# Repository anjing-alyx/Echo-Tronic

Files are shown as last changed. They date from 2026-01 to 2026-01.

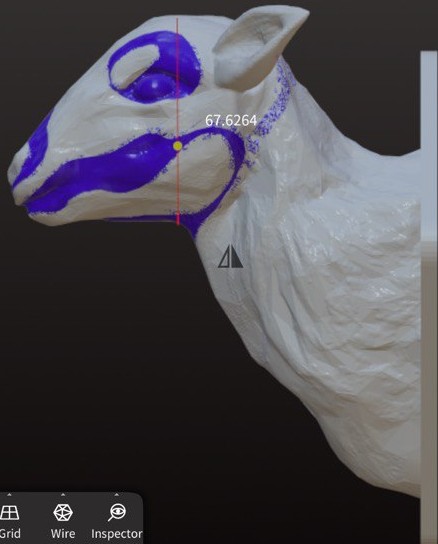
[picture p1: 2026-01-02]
Concept Art/NomadSculpt.jpg

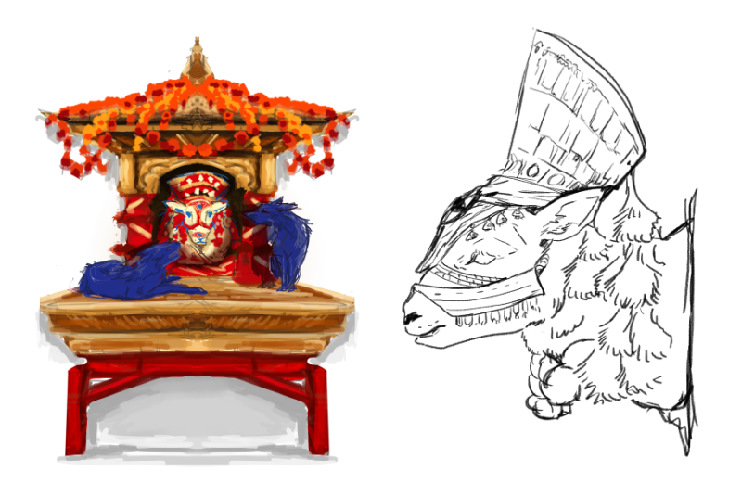
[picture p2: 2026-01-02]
Concept Art/Lamb_worship_conceptart.png

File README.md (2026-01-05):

README [WIP]
Translating human facial motion into physical animatronic movement in real time using Mediapipe API, Arduino and PCA9865. 

1. [What is Echo-Tronic](#What-is-Echo-Tronic)

2. [How does it work](#How-does-it-work)
<br/> 2.1 [Hardware](##Hardware)
<br/> &nbsp; 2.1.1 [Echo-Tronic (a.k.a AnimaBarong) Design](##Echo-Tronic-(a.k.a-AnimaBarong)-Design)
<br/> &nbsp; 2.1.2 [Arduino and PCA9685](###Arduino-and-PCA9685)
<br/> 2.2 [Software](##Software)
<br/> &nbsp; 2.2.1 [Servo Angle Calculation](###Servo-Angle-Calculation)
<br/> &nbsp; 2.2.2 [MediaPipe Facial Tracking](###MediaPipe-Facial-Tracking)
<br/> &nbsp; 2.2.3 [Arduino Serial Communication](###Arduino-Serial-Communication)

3. [What is included](#What-is-included)

4. [Final Notes:](#Final-Notes)

# What is Echo-Tronic:
Echo-Tronic (a.k.a AnimaBarong) is a personal project intending to simplify animatronic facial control from 2-4 operators controlling various facial features to one animatronic rig "echoing" an actor's performance using facial tracking. In a standard rig for facial animatronics there may be 6-20+ servos depending on complexity of expression. As humans only have two hands and 10 fingers, to control 20+ servos simultaneously using RC controllers is a bit tricky- hence the 2-6+ puppeteers manning an animatronic. 

The goal of this project is to reduce manpower required to operate animatronics, allow for more organic acting/performance, and moving the servos in real-time. This, of course, also has use in the field of social robotics and human-robot interaction- however, theme park animatronics for the use case is much more fun. 

# How does it work:
## Hardware
### Echo-Tronic (a.k.a AnimaBarong) Design
The design for the animatronic initially came from a character of mine based on the [Balinese Barong](https://en.wikipedia.org/wiki/Barong_(mythology)) hence the "a.k.a", it has since changed to a sheep head which was inspired by Weta's work on the [Black Sheep Movie](https://www.wetaworkshop.com/projects/black-sheep) and the internal mechanisms based on Gustav Hoegan's work on a [Bison head in a super glue advert](https://www.biomimicstudio.org/showreel). 

All the internal structures were modelled and assembled on SolidWorks as well as 3D printed using a Bambu X1C and PLA Filament. Non-printed parts include:
1. MG90S servos (x11)
2. Various M2.5-M3 Screws
3. Paperclips and wires
4. Electronics

The internal structure was based of a lamb head I sculpted on NomadSculpt for the next step which is a test-skin. But this is an engineering documentation not model-making documentation- so I will leave the foam skin for later. The design goal was to create a modular structure that was easy to assemble and reassemble for repairs while being easy to fabricate both on the 3D printer and machine (although that part remains to be optimized). 

### Arduino and PCA9685
I use Arduino as my testbed and PCA to control my 11 servos. They are great tools for testing- plus the only things available at home.

## Software
### Servo Angle Calculation
Initially this was done via inverse kinematics however the way euclidean distance was calculated provided inaccurate results- hence why a ratio based method was used with some hard-coded distances set in the code to calculate the servo angles. The simple calculation basically allowed for easier tuning (provided you know how to code) and less computation. I also rounded each of the angles calculated to integers that were either multiples of 2 and 5 to reduce the sensitivity of the servos when moving. 

In the future, potentially for more advanced social robots with feedback loops and the need for reliable/adaptive movement- inverse kinematics with servo feedback will be used. 

### MediaPipe Facial Tracking
[MediaPipe Face Landmark Recognition](https://ai.google.dev/edge/mediapipe/solutions/vision/face_landmarker) is the machine learning portion that detects the face and provides the coordinates for facial tracking. The distance between points such as the most top and most bottom part of the eye, is now used to calculate approximately how much the servo moves. 

<p align="center">MP Face Mesh with indices</p>
<p align="center">Fig. 1 MediaPipe Face Mesh with Indices Reference </p>

### Arduino Serial Communication
For now, the head still had an umbilical cord to the computer for control however since what Python sends via serial connection is a 22 bit string of servo angles, the order of which is associated to the servos pin-outs on the PCA9685. This packet of information can theoretically be wirelessly transmitted via RC which is the future plan of the work. 

# What is included
In this repository what is included is the most up to date working code and the .stl files for the animatronic hardware. No Solidworks Files will be shared.

# Final Note
Have fun looking around, this is ultimately a passion project in the somewhat declining trade of animatronics and sfx in movies. If you do use this as inspiration or the code for whatever reason, please credit and let me know because I'd love to see where it ends up. There are still a lot of bugs I am fixing as an amateur coder; sorry in advance- I'll fix them soon or whenever I get the time to!

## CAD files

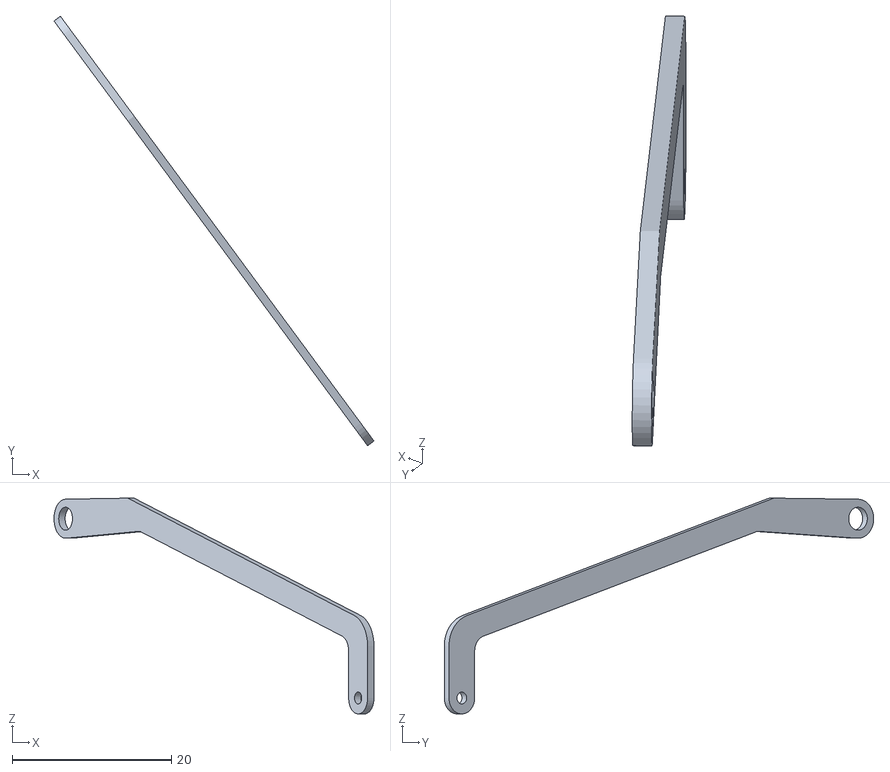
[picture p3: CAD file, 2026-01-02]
Hardware Files/Eye Assembly/EYE_LINKAGE_L.STL
40.1 x 53.9 x 27.1

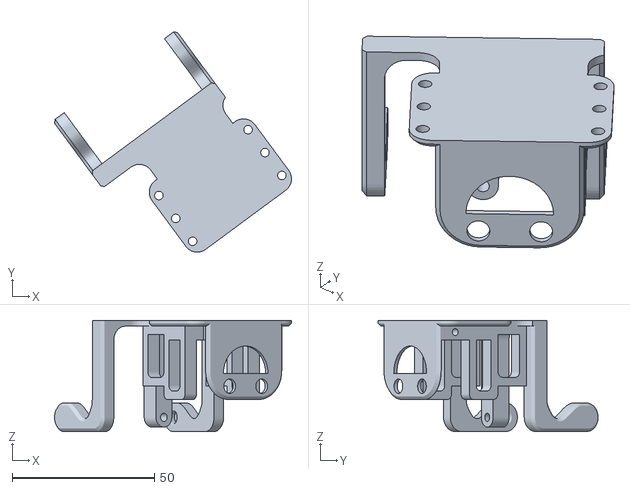
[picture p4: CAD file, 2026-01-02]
Hardware Files/Eye Assembly/Mirror/M_EYE_SERVOHOLDER.STL
83.4 x 77.5 x 39.0

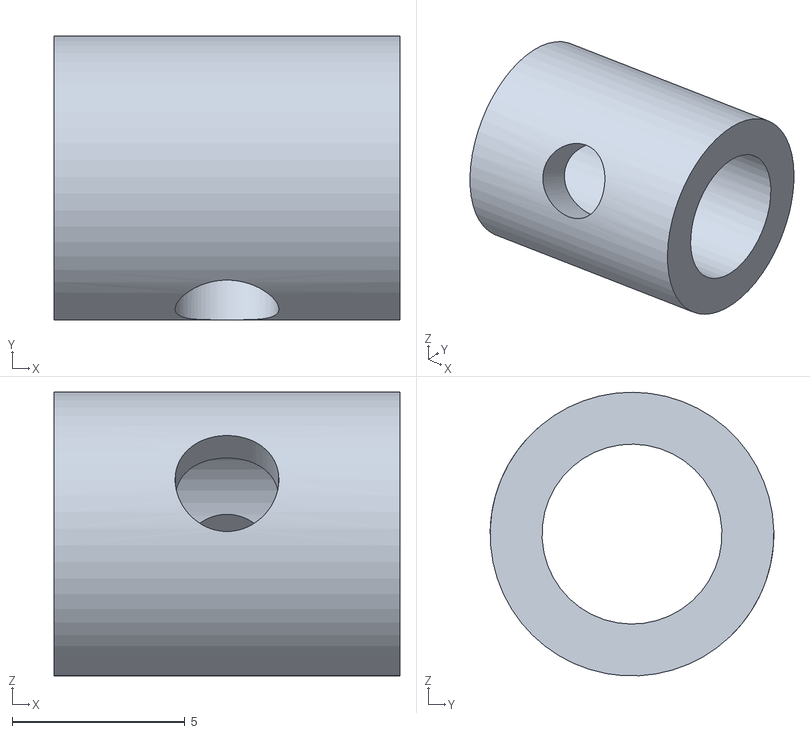
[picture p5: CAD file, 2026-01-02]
Hardware Files/LOWER JAW ROD SPACER.STL
10.0 x 8.20 x 8.19

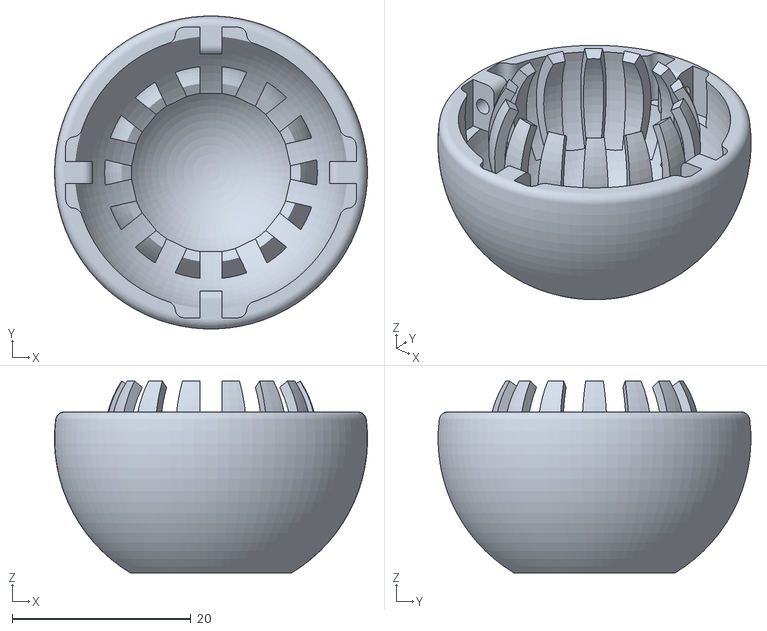
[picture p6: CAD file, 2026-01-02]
Hardware Files/Eye Assembly/EYE_EYEBALL.STL
35.0 x 35.0 x 21.4

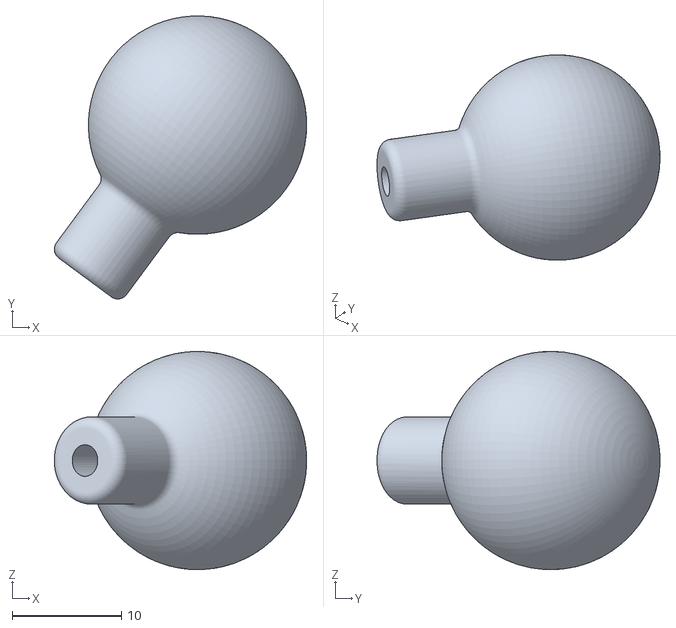
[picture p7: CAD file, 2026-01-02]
Hardware Files/Eye Assembly/Mirror/M_EYE_BALLJOINT.STL
23.1 x 25.9 x 20.0

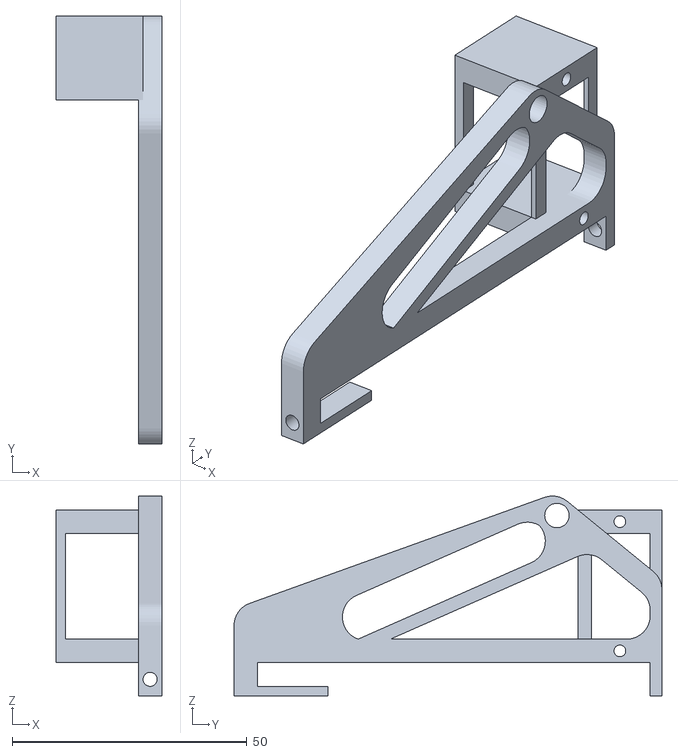
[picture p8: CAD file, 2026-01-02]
Hardware Files/M_LOWERJAW_SERVOHOLDER.STL
22.5 x 91.1 x 42.6

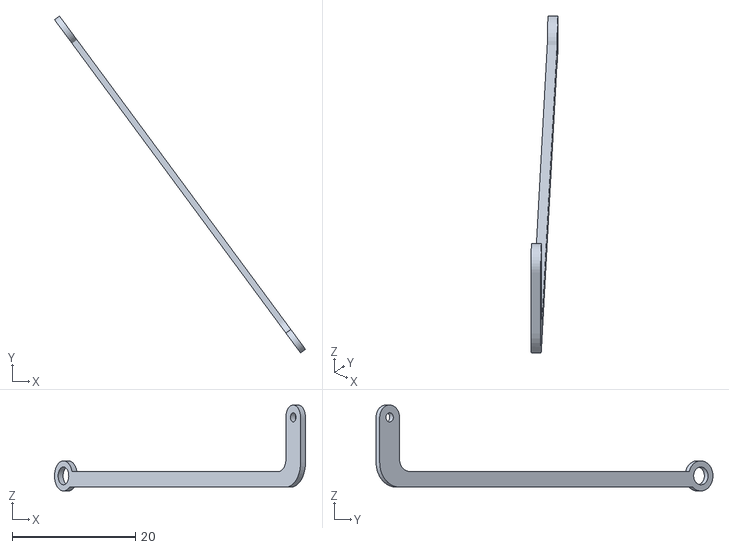
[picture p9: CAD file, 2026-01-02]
Hardware Files/Eye Assembly/EYE_LINKAGE_U.STL
40.7 x 54.6 x 13.9

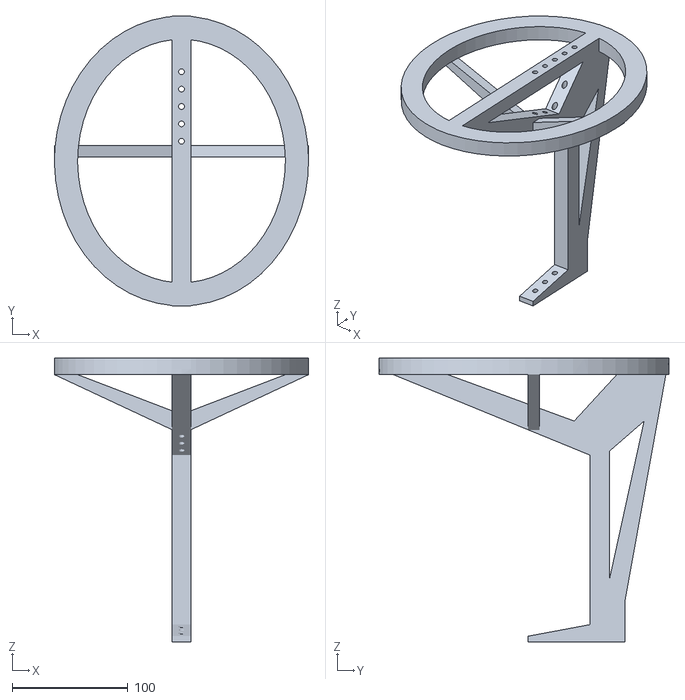
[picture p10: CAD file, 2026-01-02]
Hardware Files/TEMP_HEADSTAND.STL
219.2 x 250.0 x 245.0

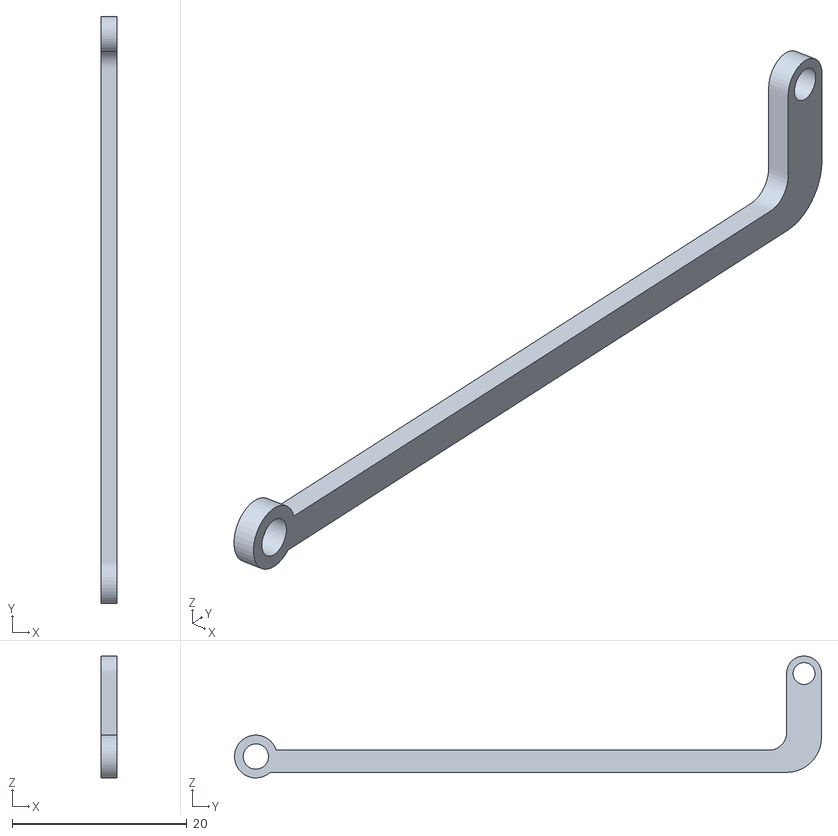
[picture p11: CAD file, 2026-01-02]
Hardware Files/Eye Assembly/EYE_EYELID_UPPER.STL
1.80 x 67.2 x 13.9

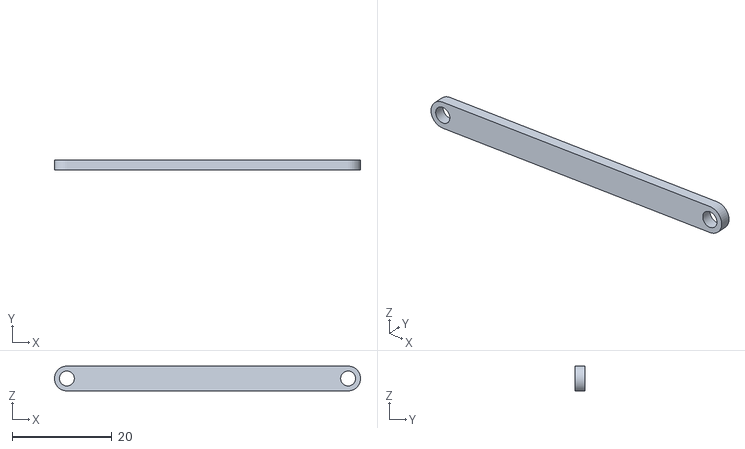
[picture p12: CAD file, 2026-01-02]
Hardware Files/NOSE_L3.STL
61.5 x 2.00 x 5.00

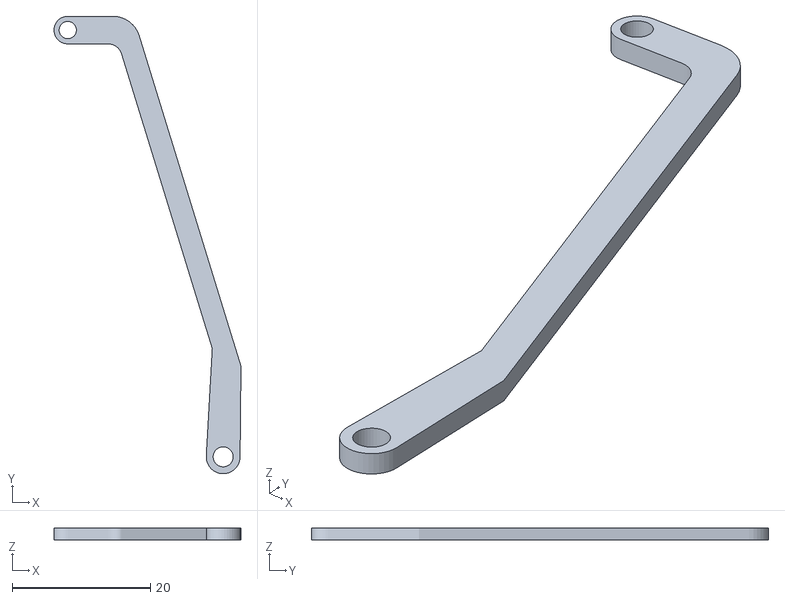
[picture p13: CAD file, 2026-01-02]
Hardware Files/Eye Assembly/EYE_EYELID_LOWER.STL
27.1 x 66.2 x 1.80

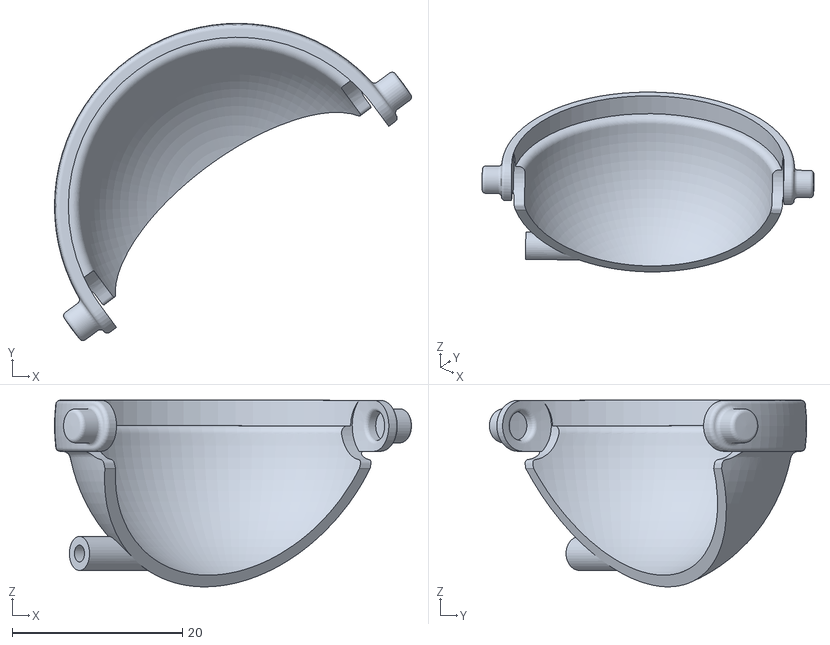
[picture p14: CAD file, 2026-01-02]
Hardware Files/Eye Assembly/Mirror/M_EYELID_UPPER.STL
41.9 x 37.3 x 21.9

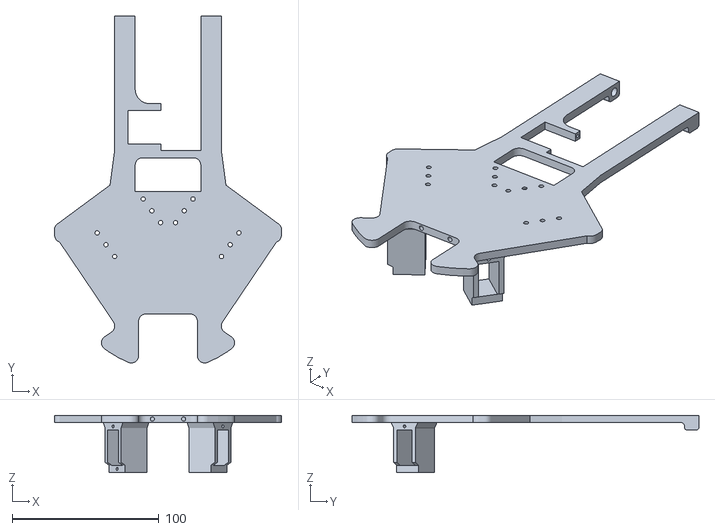
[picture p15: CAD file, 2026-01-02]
Hardware Files/HEAD_BASE.STL
154.9 x 236.4 x 39.0

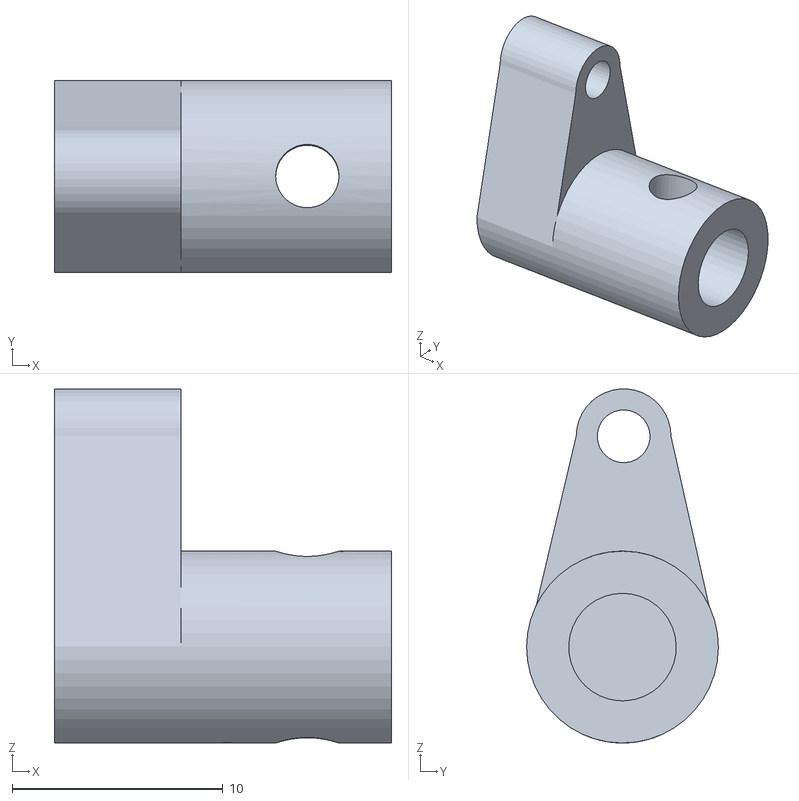
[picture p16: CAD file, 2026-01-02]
Hardware Files/LOWERJAW ROD HUB.STL
16.0 x 9.10 x 16.8

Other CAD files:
Hardware Files/EYEBROW_LINKAGE.STL
Hardware Files/Eye Assembly/EYE_SERVOHOLDER.STL
Hardware Files/Eye Assembly/Mirror/M_EYELID_LOWER.STL
Hardware Files/HEAD_MOUNT.STL
Hardware Files/LOWER JAW.STL
Hardware Files/LOWERJAW-SERVO LINKAGE.STL
Hardware Files/LOWERJAW_SERVOHOLDER.STL
Hardware Files/NECK.STL
Hardware Files/NOSE.STL
Hardware Files/NOSE_L2.STL

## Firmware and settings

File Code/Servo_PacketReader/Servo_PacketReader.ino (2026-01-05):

#include <Wire.h>
#include <Adafruit_PWMServoDriver.h>

Adafruit_PWMServoDriver pwm = Adafruit_PWMServoDriver(0x40);

#define SERVOMIN 125 // Minimum pulse length (0 degrees)
#define SERVOMAX 625  // Maximum pulse length (180 degrees)
#define N_SERVOS 11   // Total servos

void setup() {
  Serial.begin(115200);
  pwm.begin();
  pwm.setPWMFreq(50); // Servos ~50 Hz

  // Initialize all servos to neutral 90°
  for(int i=0; i<N_SERVOS; i++){
    pwm.setPWM(i, 0, angleToPulse(90));
  }
}

// Convert angle (0-180) to PWM pulse
int angleToPulse(int angle) {
  angle = constrain(angle, 0, 180);
  return map(angle, 0, 180, SERVOMIN, SERVOMAX);
}

void loop() {
  if(Serial.available()){
    static String buffer = "";
    char c = Serial.read();

    if(c == '<'){
      buffer = ""; // start marker
    } 
    else if(c == '>'){
      // end marker -> parse packet
      int count = 0;
      char *token = strtok((char*)buffer.c_str(), ",");
      while(token != NULL && count < N_SERVOS){
        int angle = atoi(token);
        pwm.setPWM(count, 0, angleToPulse(angle));
        token = strtok(NULL, ",");
        count++;
      }
    } 
    else {
      buffer += c;
    }
  }
}

/* Servo Mapping (Python packet indices):
   S0: ReyeX       -> Channel 0
   S1: LeyeX       -> Channel 1
   S2: ReyeY       -> Channel 2
   S3: LeyeY       -> Channel 3
   S4: Rblink      -> Channel 4
   S5: Lblink      -> Channel 5
   S6: Rebrow      -> Channel 6
   S7: Lebrow      -> Channel 7
   S8: Right Mouth -> Channel 8
   S9: Left Mouth  -> Channel 9
   S10: Nose       -> Channel 10
*/

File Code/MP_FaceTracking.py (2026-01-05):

# -*- coding: utf-8 -*-
"""
Created on Fri Dec 19 16:03:16 2025

@author: Adel Lee (SYK)
"""
import math
import serial
import time
import mediapipe as mp
import cv2
import tkinter as tk
from threading import Thread
import numpy as np

# ---------------------------
# Servo setup (angle and variable definition)
# ---------------------------
### Author's Note: Servo start angle/min angle is always in closed position. Left Servos are always mirrored ###

rx_min, rx_max = 72, 108 ## Right Eye X-Direction - Servo 0 (-)R, (+)L
lx_min, lx_max = 72, 108 ## Left Eye X-Direction - Servo 1 (-R), (+)L

ry_min, ry_max = 76.5, 103.5 ## Right Eye Y-Direction - Servo 2 (-)D, (+)U
ly_min, ly_max = 76.5, 103.5 ## Left Eye Y-Direction - Servo 3 (-)U, (+)D

rb_min, rb_max = 20, 90 ## Right Eye Blink - Servo 4 (-)U
lb_min, lb_max = 90, 140 ## Left Eye Blink - Servo 5 (+)U

reb_min, reb_max = 75, 105 ## Right Eyebrow - Servo 6 (-)D, (+)U  - Index 295 track relative to midpoint of eye_width
leb_min, leb_max = 75, 105 ## Left Eyebrow - Servo 7 - (-)U, (+)D - Index 55

m1_min, m1_max = 90, 180 ## Right Mouth Servo - Servo 8 (-)U, (+)D
m2_min, m2_max = 0, 90 ## Left Mouth Servo - Servo 9 (-)D, (+)US

nose_min, nose_max = 81,120 ## Nose Servo - Servo 10 (-)U, (+)D

## Define Horizontal Eye Distance as a scale bar for mm conversion ##
horizontal_eye = 32

SENSITIVITY = 6             # Max deviation from center, Adjust this setting to increase range of angle
SMOOTH_ALPHA = 0.9           # smoothing factor, Adjust this setting if smoothing is less or more needed 

# Calibration storage
calib = {"x_min": None, "x_max": None, "y_min": None, "y_max": None}

# Mediapipe
mp_face_mesh = mp.solutions.face_mesh

selected_indices = [386, 374, 145, 159, 13, 14, 393, 269,
                    33, 133, 362, 263, 468, 473, 282, 442,222,52]

# ---------------------------
# Serial setup (safe) 
# ---------------------------
SERIAL_PORT = 'COM5'   # change this as needed
BAUD = 115200

arduino = None
try:
    arduino = serial.Serial(SERIAL_PORT, BAUD, timeout=0.1)
    time.sleep(2)  # wait for Arduino reset
except Exception as e:
    print(f"Warning: couldn't open serial port {SERIAL_PORT}: {e}")
    arduino = None

def pack_send(packet):
    """Send packet to Arduino with start/end markers and integer angles.
       Packet is list/tuple of numeric values.
    """
    if arduino is None:
        # For debugging without Arduino connected
        print("Would send:", packet)
        return
    # Ensure integers and clamp 0-180 (typical servo range)
    ints = [max(0, min(180, int(round(x)))) for x in packet]
    msg = "<" + ",".join(map(str, ints)) + ">"
    try:
        arduino.write(msg.encode())
    except Exception as e:
        print("Serial write error:", e)
        
# ---------------------------
# Utility Functions
# ---------------------------
# Source - https://stackoverflow.com/a
# Posted by Alok Singhal, modified by community. See post 'Timeline' for change history
# Retrieved 2025-12-29, License - CC BY-SA 4.0, for "def myround" only

def myround(x, base=2):
    return base * round(x/base)

def eu_dist(p1, p2):
    x1, y1 = p1
    x2, y2 = p2
    return math.sqrt((x2 - x1)**2 + (y2 - y1)**2)


eye_max = {"L": 0.0, "R": 0.0}  # store per eye

def theta14(p1,p2,sf):
    mm_convert=sf*eu_dist(p1,p2)
    eye_ratio = (mm_convert/(0.6*horizontal_eye))*90
    print(eye_ratio)
    if eye_ratio < 30:
        return 90
    elif eye_ratio >= 100:
        return 170
    else:
        return myround(eye_ratio)+90

def scale_factor (coords):
    lcorner, rcorner = coords[33], coords[133]
    eye_width = rcorner[0] - lcorner[0]
    return horizontal_eye/eye_width

##Top lip as anchor/ground for eu-dist calculation.
def mouth(m1, m2, sf):
    mdist = eu_dist(m1, m2)
    mdist_mm = mdist*sf
    mangle = math.degrees(math.asin(mdist_mm/140))*3 ## 140mm is the Length of Current Mouth
    m1angle = m1_min + mangle # Right mouth angle      
    return myround(m1angle)

def eyebrow(brow, eye, sf, mi, ma):
    edist = eu_dist(eye,brow)
    eangle = (myround(edist*sf,base = 5)/(1.2*horizontal_eye))*abs(ma-mi)+mi-16
    if eangle < 90 and eangle > 85:
        return 90
    if eangle > 90:
        return ma
    else:
        return myround(eangle, base =5)
    
def nose(l1, l2, sf):
    ldist = eu_dist(l1, l2)
    ldist_mm = ldist*sf 
    return myround(math.degrees(math.asin(ldist_mm/65))*3 + nose_min) ## 65mm is length of nose pivot to servo (Length of nose linkage)


# ---------------------------
# Landmark Extraction
# ---------------------------

def get_landmarks(frame, face_mesh):
    h, w, _ = frame.shape
    rgb = cv2.cvtColor(frame, cv2.COLOR_BGR2RGB)
    results = face_mesh.process(rgb)
    coords = {}
    if results.multi_face_landmarks:
        for face_landmarks in results.multi_face_landmarks:
            for idx in selected_indices:
                lm = face_landmarks.landmark[idx]
                coords[idx] = (int(lm.x*w), int(lm.y*h))
    return coords

# ---------------------------
# Continuous Calibration
# ---------------------------

def update_calibration(iris_ratio):
    # iris_ratio = (x_ratio, y_ratio)
    x, y = iris_ratio
    if calib["x_min"] is None or x < calib["x_min"]: calib["x_min"] = x
    if calib["x_max"] is None or x > calib["x_max"]: calib["x_max"] = x
    if calib["y_min"] is None or y < calib["y_min"]: calib["y_min"] = y
    if calib["y_max"] is None or y > calib["y_max"]: calib["y_max"] = y

# ---------------------------
# Eye Tracking
# ---------------------------

def process_eye_tracking(coords, prev_angles, eye="left"):
    if eye == "left":
        lcorner, rcorner = coords[33], coords[133]
        iris = coords[468]
    elif eye == "right":
        lcorner, rcorner = coords[362], coords[263]
        iris = coords[473]

    # Avoid division by zero
    eye_width = rcorner[0] - lcorner[0]
    eye_height = rcorner[1] - lcorner[1]
    if eye_width == 0: eye_width = 1
    if eye_height == 0: eye_height = 1

    iris_x_ratio = (iris[0] - lcorner[0]) / eye_width
    iris_y_ratio = (iris[1] - lcorner[1]) / eye_height

    # Update calibration
    update_calibration((iris_x_ratio, iris_y_ratio))

    # Map to servo angles
    if None not in calib.values():
        norm_x = np.interp(iris_x_ratio, [calib["x_min"], calib["x_max"]],
                           [90-SENSITIVITY, 90+SENSITIVITY])
        norm_y = np.interp(iris_y_ratio, [calib["y_min"], calib["y_max"]],
                           [90-SENSITIVITY, 90+SENSITIVITY])
    else:
        norm_x, norm_y = 90, 90

    # Apply smoothing
    smoothed_x = SMOOTH_ALPHA*norm_x + (1-SMOOTH_ALPHA)*prev_angles[0] ## Additional 1.2sf for more exaggerated movements
    smoothed_y = SMOOTH_ALPHA*norm_y + (1-SMOOTH_ALPHA)*prev_angles[1]

    return smoothed_x, smoothed_y
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

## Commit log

2026-01-02 feat: V1 Echo-Tronic File Upload
    Upload of Version 1. Echo-Tronic Files with Concept art, STL Files and Facial Tracking Code (Arduino and Python).
    [EYEBROW_LINKAGE.STL, EYE_BALLJOINT.STL, EYE_EYEBALL.STL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]
2026-01-05 feat: additional video input type
    Choice to upload or livestream via webcam has been added with additional sample videos and demo.
2026-01-07 Add V1 Hardware Demo Video
    Hardware demo showing facial tracking to servo movement from a sample video.
